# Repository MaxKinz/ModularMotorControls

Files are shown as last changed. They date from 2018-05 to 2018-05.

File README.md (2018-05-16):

"# ModularMotorControls" 
This is going to be a motor control project loosely based on the famous "VESC" project by benjamin vedder. 
So why another open source motor controller ? Well-mainly for modularity
The ultimate goal is to have a controller that does exactly what you need for a good price on every level wether you need to move some small 4000kv hobby rc motor or a full industrial Servo at 400V. Obviously the hardware required for the servo would be overkill and too expensive for the small motor while having additional limitations. 
Therefore hardware is going to be split into 3 categories that first have to be defined with all their requirements resulting in interfaces. A design requirement is that every implementation of one of those categories is compatible with every implementation of the two others so if for instance 3 implementations of each exist one could configure 27 different controllers. There will however be compatibility ranges between category 2 and 3 as it is impossible to completely seperate them. 

Here are the the categories :
  1. A logic board containing at least an STM32 microprocessor 
    -Variants with more or less calc power (closed loop control vs. open loop, BLDC or FOC..... Position/speed etc control) 
    -interfaces (CAN,I²C,UART,SPI....)
    -peripherals (IMUs,Bluetooth,ZigBee,LoRa or whatever comes to mind)    
    -may also be implemented breakout boards for readily available ebay bords
  
  2. A predriver stage containing MOSFET drivers as well as all the voltage "grooming" buck and boost converters (mainly different   
     different target Voltages)
     - "all in one"- solutions like the TI DRV8302
     - or discrete mosfet drivers and buck converters shunt amps 
     
  3. A power stage containing the main leads, the big input filter caps, and of course the MOSFETs/IGBTs, shunts,temp sense (mainly 
     different target currents but also voltages) 
     - all MOSFETs on one side or using both sides - different temp sensors,
     - SMD, THT , radiators,etc...
  
So as you can see I mainly just split up the usual components of a motor driver - big whoop - so what is this about ? 
Well - I would love to have defined interfaces between those parts. It would make it easy to reuse software that is otherwise rewritten over and over. It would also make it loads cheaper if by overloading your robot you yet again blew up a driver - and now conveniently only replace the power board (or if you are not so lucky power and predriver) 
All of my work on this will be open source. Since I plan on repurposing some of the VESC software which is based on ChibiOS and ChibiOS is GPL I might be forced to use GPL for the first iteration. However I am not a big fan of the agressive approach the GPL takes on open source which, if you are honest, resticts projects to hobby use as no employer I know wants his/her IP he payed you to create out there....so I would love to write some code under, for example, Apache liscense later in the process so truely anyone can use the controller even if you use it for work.

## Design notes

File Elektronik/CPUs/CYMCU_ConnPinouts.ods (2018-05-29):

 | Hall Sensors | Inc. Encoders | Mag enc. | I²C (gen.P.) | SPI (gen.P) | STEP/DIR | UART | AnalogIn
MCU Pin | PB6,PB7,PC11 | PB6,PB7,PC11 | PB6,PB7,PC11 | PA4,PA7 | PA4,PA5,PA6,PA7 | PA4/PA5 | PA4,PA7 | PC2
Interface | PIN HEADER 5x1 | PIN HEADER 5x1 | PIN HEADER 5x1 | PinHeader6x1 | PinHeader6x1 | PinHeader6x1 | PinHeader6x1 | PinHeader2x1
Notes | Only one sensor and one interface at a time ! - there will be two sensor ports though with filter (for Hall) and without (for incremental) but only one control signal connector

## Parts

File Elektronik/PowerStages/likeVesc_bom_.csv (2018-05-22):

Component | Description | Part | References | Value | Footprint | Quantity Per PCB | Datasheet
1 | Connector, double row, 02x10, pin header | CONN_02X10 | J1 | CONN_02X10 | Pin_Header_Straight_2x10_Pitch2.54mm | 1
2 | 2-pin screw terminal connector | Screw_Terminal_1x02 | J3 J4 | Screw_Terminal_1x02 | TerminalBlock_Altech_AK300-2_P5.00mm | 2
3 | 3-pin screw terminal connector | Screw_Terminal_1x03 | J2 | Screw_Terminal_1x03 | TerminalBlock_Altech_AK300-3_P5.00mm | 1
4 |  | MOSFET_N | Q1 Q2 Q3 Q4 Q5 Q6 | IRFS7530 | D2PAK-7-GDS | 6
5 |  | R-RESCUE-BLDC_4 | R3 R7 R11 | 39k | SMD-0603_r | 3
6 |  | R-RESCUE-BLDC_4 | R1 R2 R5 R6 R9 R10 | 4R7 | SMD-0603_r | 6
7 |  | SHUNT | R4 R8 | SHUNT | WSLP2726 | 2
Component Groups: | 7
Component Count: | 21
Fitted Components: | 21
Number of PCBs: | 1
Total components: | 21
Schematic Version:
Schematic Date:
BoM Date: | 22.05.2018 20:13:28
Schematic Source: | F:/git/ModularMotorControl/Elektronik/PowerStages/likeVesc.sch
KiCad Version: | Eeschema 4.0.6

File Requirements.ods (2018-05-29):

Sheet: Overview
This Document will hold the requirements for the Interfaces between the three categories of boards that make up a ModMot Controller It will also contain additional sheets for each implementation of any of the categories as made for a targeted application
 | Connections between logic and driver
 | going into logic | Name | Pin Number | Voltage/ref | Reason | Conclusion so far there are 18 connections necessary for the interface. As obviously some things may be added in the future a 2x15 pin header is chosen as the standard connection – the first 15 for incoming and the seconf 15 for outgoing connections on each board – pin numbers as in here top to bottom 1=VCC; 16=M1H
 |  | Vcc | 1 | 3.3V | MCU+Periph Power
 |  | Vsensors | 2 | 5V | for Periphery req. 5V
 |  | VsensHigh | 3 | 12V | for higher Voltage periphery such as inductive sensors or incremental encoders
 |  | GND | 4 | 0V | Ground reference
 |  | TempMosfets | 5 | SIGNAL | MosfetTempsense
 |  | VinSense | 6 | SIGNAL | Sense input voltage
 |  | SHUNT1 | 7 | SIGNAL | Current sense
 |  | SHUNT2 | 8 | SIGNAL | Current sense
 |  | SHUNT3 | 9 | SIGNAL | Current sense
 |  | Vsense1 | 10 | SIGNAL | Voltage sense
 |  | Vsense2 | 11 | SIGNAL | Voltage sense
 |  | Vsense3 | 12 | SIGNAL | Voltage sense
 | going into driver
 |  | M1H | 16 | FET SIGNAL | Switch Line one High side
 |  | M1L | 17 | FET SIGNAL | switch line one low side
 |  | M2H | 18 | FET SIGNAL | switch line two high side
 |  | M2L | 19 | FET SIGNAL | switch line two low side
 |  | M3H | 20 | FET SIGNAL | switch line three high side
 |  | M3L | 21 | FET SIGNAL | switch line three low side
 |  | Enable | 22 | SIGNAL | may be required by some drivers
 | Other Connections : | There may be plenty other connections such as Hall sensors, different input modes etc. but that is beyond the scope of this document. Only the essentials are recorded here as the goal is a standard cnnector layout used in different applications.
 | Connections from driver to power
 |  | M1H | 1 | FET DriveSignal |  | So far there are 16 connectinos and a 2x10 pin header is chosen. The power connections are missing as the driver outputs are already at the limit of a standard pin header so that a separate connection is needed
 |  | M1L | 2 | FET DriveSignal
 |  | M2H | 3 | FET DriveSignal
 |  | M2L | 4 | FET DriveSignal
 |  | M3H | 5 | FET DriveSignal
 |  | M3L | 6 | FET DriveSignal
 | Connections from power to driver
 |  | SH_1A | 11 | Shunt1+/Signal | if shuntamps are in Driver this is + else it carries the signal
 |  | SH_1B | 12 | Shunt1- | Shuntamps on Power -NC
 |  | SH_2A | 13 | Shunt2+/Signal
 |  | SH_2B | 14 | Shunt2-
 |  | H1VS | 15
 |  | H1Low | 16
 |  | H2VS | 17
 |  | H2LOW | 18
 |  | H3VS | 19
 |  | H3Low | 20

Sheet: Requirements_Logic_board
 |  |  | CPUs |  |  |  | Features |  |  | Interfaced accessories |  |  |  |  | Control interfaces
Design goals: | Description | Cheap/affordable | Use Ebay Board | STM32F1 /SoftwareBasis AutoQuad ESC32 | STM32F4 Software Basis VESC | STM32F4 Software Basis Odrive | Position Control | FOC | Dual Motor | Hall Sensors | Inc. Encoders | Mag enc. | I²C (gen.P.) | SPI (gen.P) | CAN | SPI | I²C | STEP/DIR | UART | ANALOG
Design 1 | BreakoutBoard for Bluepill to implement very cheap low power Servo controllers | x | x | x |  |  | x |  |  |  | x | x |  |  |  |  |  | x | x | -
Design 2 | BreakoutBoard for CYMCU407 | x | x |  | x |  | x | x |  | x | x | x | x | x |  |  |  | x | x | x

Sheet: PinoutsFirmwareBasis
Here we have the different pinouts for different firmwares
 |  |  |  |  | Autoquad ESC32 STM32F103 PIN Name | STM32F103 BluepillPinNumber
 | Vcc | 1 | 3.3V | MCU+Periph Power | -
 | Vsensors | 2 | 5V | for Periphery req. 5V | -
 | VsensHigh | 3 | 12V | for higher Voltage periphery such as inductive sensors or incremental encoders | -
 | GND | 4 | 0V | Ground reference | GND
 | TempMosfets | 5 | SIGNAL | MosfetTempsense | TODO
 | VinSense | 6 | SIGNAL | Sense input voltage | PA4
 | SHUNT1 | 7 | SIGNAL | Current sense | PA5
 | SHUNT2 | 8 | SIGNAL | Current sense | TODO
 | SHUNT3 | 9 | SIGNAL | Current sense | TODO
 | Vsense1 | 10 | SIGNAL | Voltage sense | PA1
 | Vsense2 | 11 | SIGNAL | Voltage sense | PA2
 | Vsense3 | 12 | SIGNAL | Voltage sense | PA3
 | M1H | 16 | FET SIGNAL | Switch Line one High side | PB6
 | M1L | 17 | FET SIGNAL | switch line one low side | PA7
 | M2H | 18 | FET SIGNAL | switch line two high side | PB7
 | M2L | 19 | FET SIGNAL | switch line two low side | PB0
 | M3H | 20 | FET SIGNAL | switch line three high side | PB8
 | M3L | 21 | FET SIGNAL | switch line three low side | PB1
 | Enable | 22 | SIGNAL | may be required by some drivers | TODO

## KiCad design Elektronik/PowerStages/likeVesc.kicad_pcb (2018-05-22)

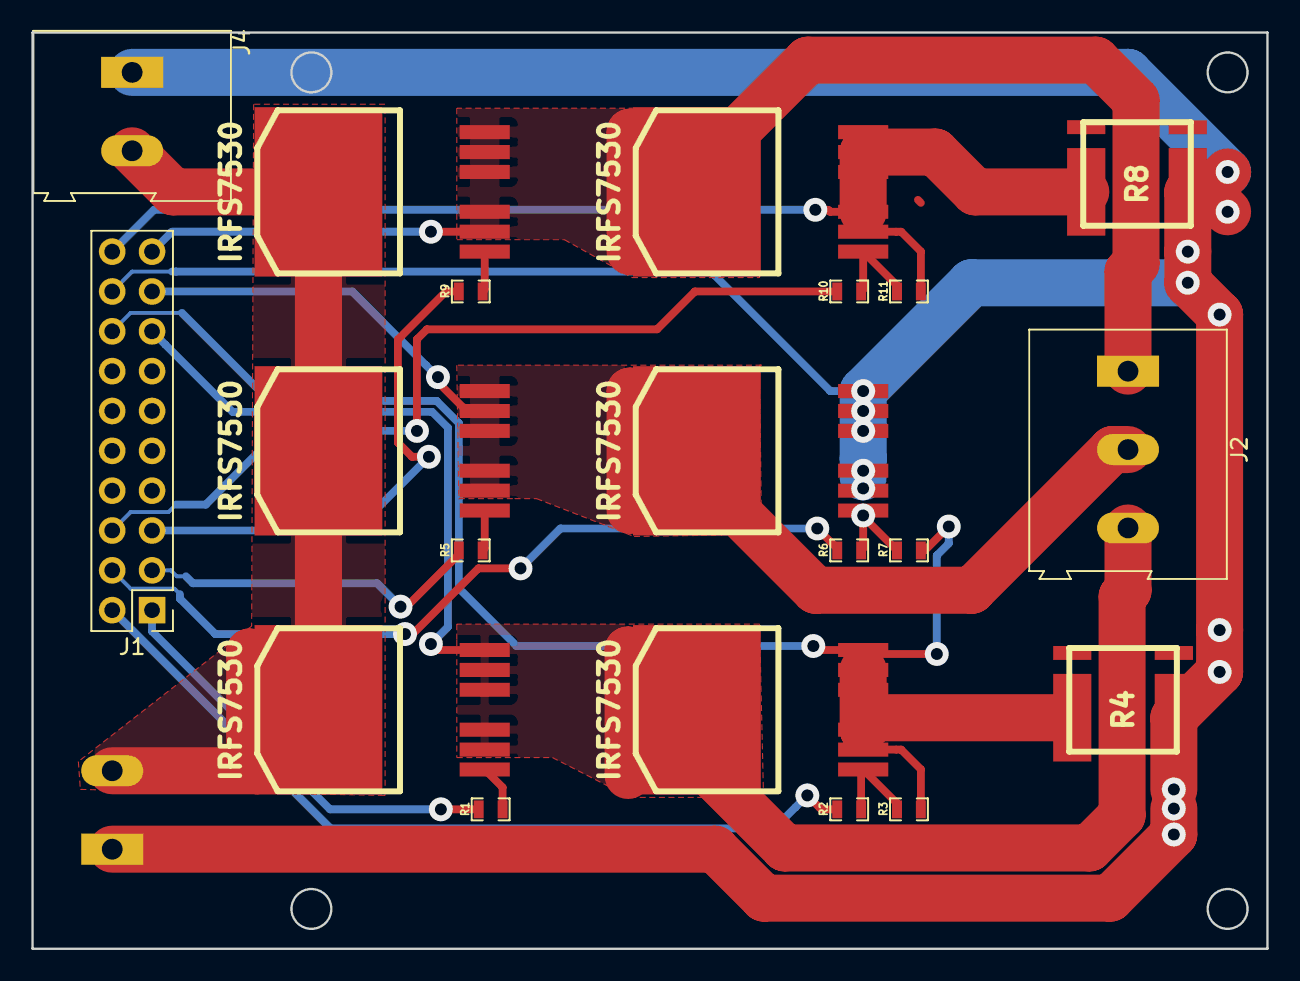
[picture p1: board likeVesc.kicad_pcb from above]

Board: 2 copper layers, 78.7 x 58.4 mm, 21 parts (1 on the bottom side), 19 nets.

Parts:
J1: CONN_02X10; Pin_Header_Straight_2x10_Pitch2.54mm
J2: Screw_Terminal_1x03; TerminalBlock_Altech_AK300-3_P5.00mm
J3, J4: Screw_Terminal_1x02; TerminalBlock_Altech_AK300-2_P5.00mm
Q1, Q2, Q3, Q4, Q5, Q6: IRFS7530; D2PAK-7-GDS
R1, R2, R5, R6, R9, R10: 4R7; SMD-0603_r
R3, R7, R11: 39k; SMD-0603_r
R4, R8: SHUNT; WSLP2726

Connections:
/BenMosfets/H1_LOW: J1.16, Q2.S, R3.1, R4.1, R7.1
/BenMosfets/H1_VS: J1.15, J2.3, Q1.S, Q2.D
/BenMosfets/H2_VS: J1.17, J2.2, Q3.S, Q4.D
/BenMosfets/H3_LOW: J1.20, Q6.S, R8.1, R11.1
/BenMosfets/H3_VS: J1.19, J2.1, Q5.S, Q6.D
/BenMosfets/M_H1: J1.1, R1.2
/BenMosfets/M_H2: J1.3, R5.2
/BenMosfets/M_H3: J1.5, R9.2
/BenMosfets/M_L1: J1.2, R2.2
/BenMosfets/M_L2: J1.4, R6.2
/BenMosfets/M_L3: J1.6, R10.2
GND: J1.18, J3.1, J4.1, Q4.S, R4.2, R8.2
unnamed: Q1.G, R1.1
unnamed: Q2.G, R2.1, R3.2
unnamed: Q3.G, R5.1
unnamed: Q4.G, R6.1, R7.2
unnamed: Q5.G, R9.1
unnamed: Q6.G, R10.1, R11.2
V_SUPPLY: J3.2, J4.2, Q1.D, Q3.D, Q5.D

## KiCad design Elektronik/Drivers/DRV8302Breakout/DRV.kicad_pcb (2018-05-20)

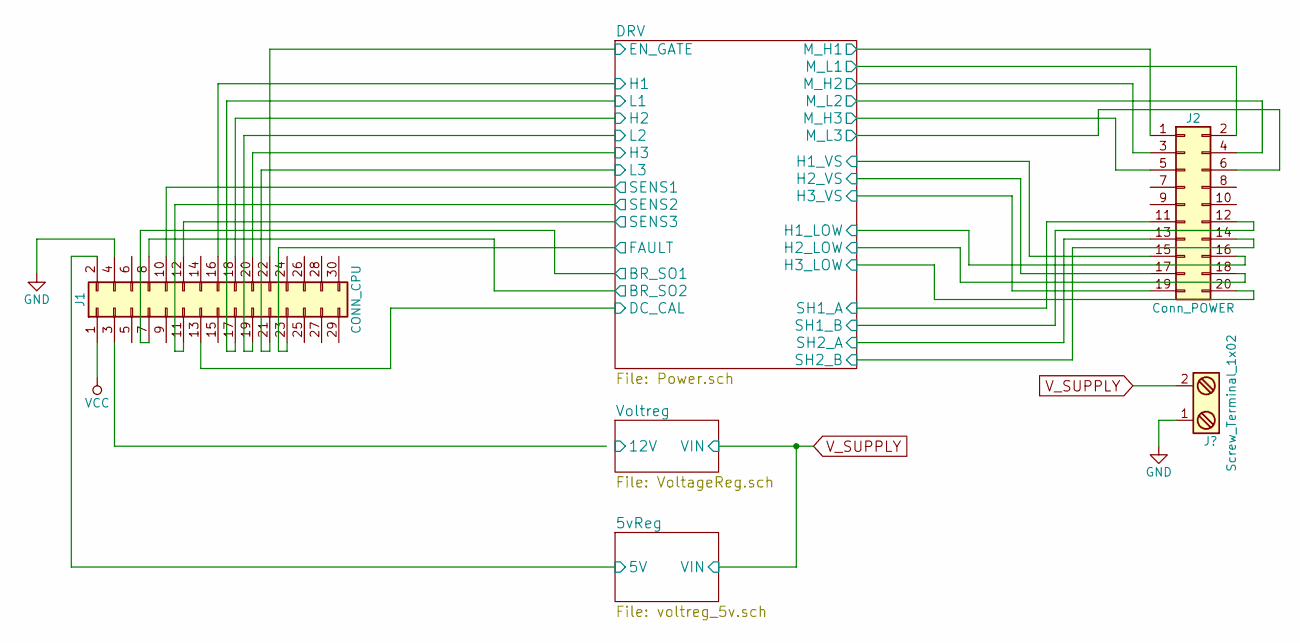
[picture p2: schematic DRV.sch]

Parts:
J1: CONN_CPU; Pin_Header_Straight_2x15_Pitch2.54mm
J2: Conn_POWER; Pin_Header_Straight_2x10_Pitch2.54mm

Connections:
/5vReg/5V: J1.2; also elsewhere on the board
/DRV/BR_SO1: J1.7; also elsewhere on the board
/DRV/BR_SO2: J1.8; also elsewhere on the board
/DRV/DC_CAL: J1.13; also elsewhere on the board
/DRV/EN_GATE: J1.22; also elsewhere on the board
/DRV/FAULT: J1.23; also elsewhere on the board
/DRV/H1: J1.16; also elsewhere on the board
/DRV/H1_LOW: J2.16; also elsewhere on the board
/DRV/H1_VS: J2.15; also elsewhere on the board
/DRV/H2: J1.18; also elsewhere on the board
/DRV/H2_LOW: J2.18; also elsewhere on the board
/DRV/H2_VS: J2.17; also elsewhere on the board
/DRV/H3: J1.20; also elsewhere on the board
/DRV/H3_LOW: J2.20; also elsewhere on the board
/DRV/H3_VS: J2.19; also elsewhere on the board
/DRV/L1: J1.17; also elsewhere on the board
/DRV/L2: J1.19; also elsewhere on the board
/DRV/L3: J1.21; also elsewhere on the board
/DRV/M_H1: J2.1; also elsewhere on the board
/DRV/M_H2: J2.3; also elsewhere on the board
/DRV/M_H3: J2.5; also elsewhere on the board
/DRV/M_L1: J2.2; also elsewhere on the board
/DRV/M_L2: J2.4; also elsewhere on the board
/DRV/M_L3: J2.6; also elsewhere on the board
/DRV/SENS1: J1.10; also elsewhere on the board
/DRV/SENS2: J1.11; also elsewhere on the board
/DRV/SENS3: J1.12; also elsewhere on the board
/DRV/SH1_A: J2.11; also elsewhere on the board
/DRV/SH1_B: J2.12; also elsewhere on the board
/DRV/SH2_A: J2.13; also elsewhere on the board
/DRV/SH2_B: J2.14; also elsewhere on the board
GND: J1.4; also elsewhere on the board
VCC: J1.1; also elsewhere on the board

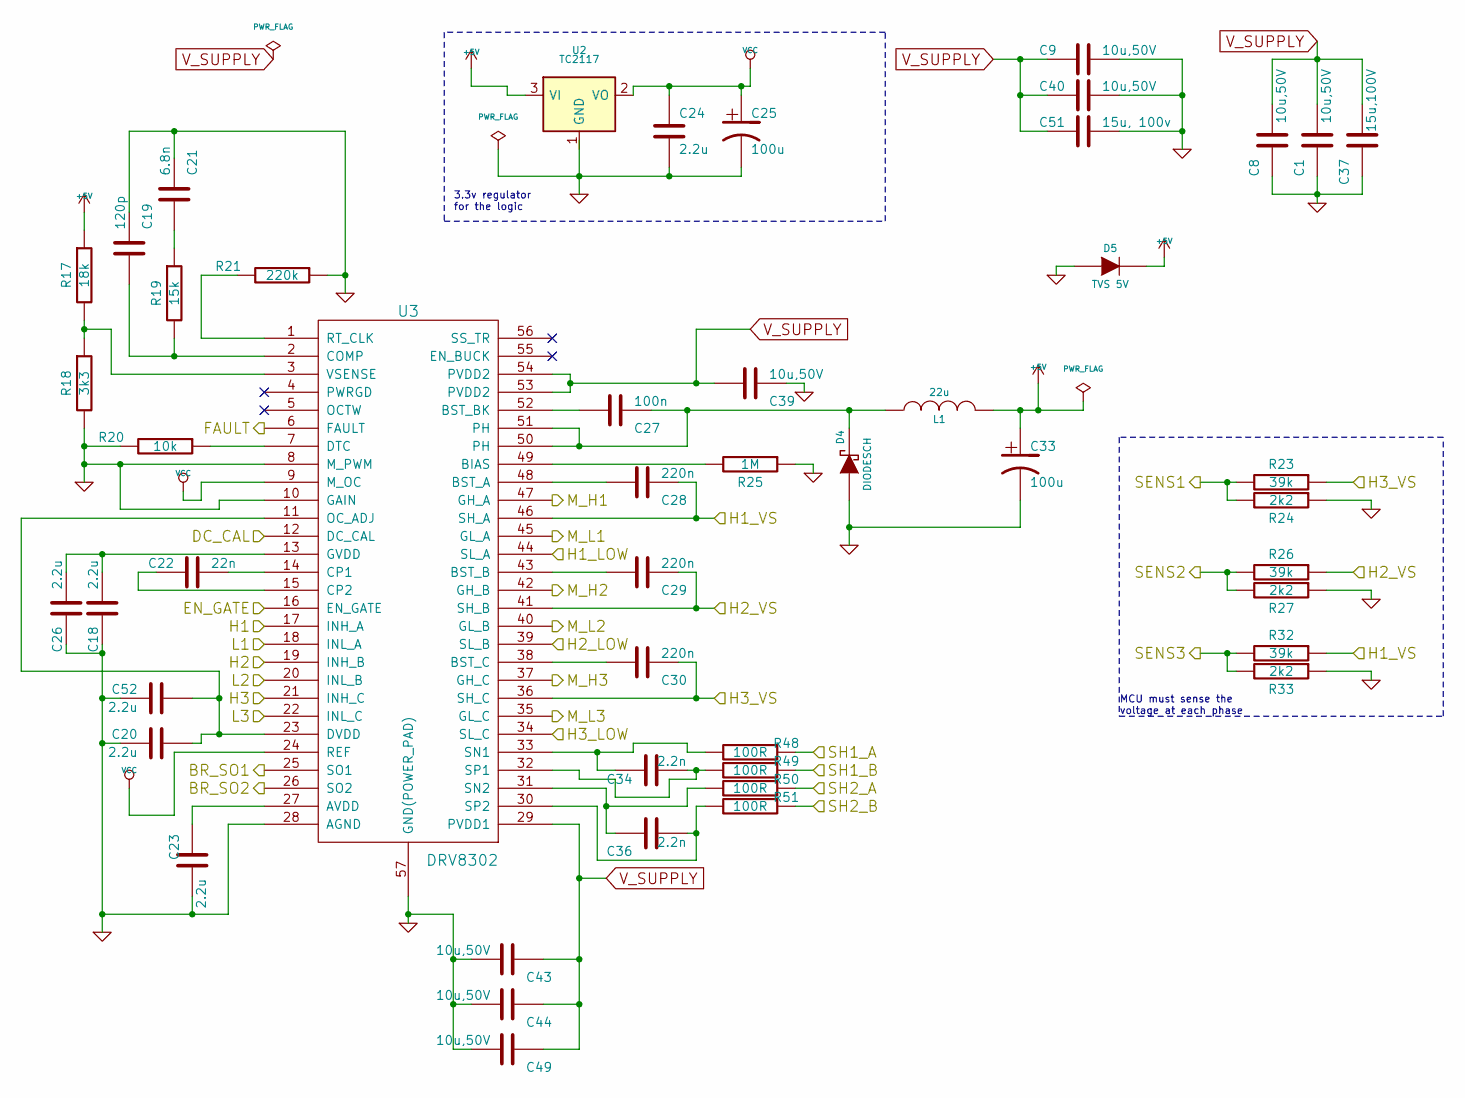
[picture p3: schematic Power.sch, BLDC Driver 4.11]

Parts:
C1, C8, C9, C39, C40, C43, C44, C49: 10u,50V; SMD-1206
C18, C20, C23, C24, C26, C52: 2.2u; SMD-0603_c
C19: 120p; SMD-0603_c
C21: 6.8n; SMD-0603_c
C22: 22n; SMD-0603_c
C25, C33: 100u; c_tant_B
C27: 100n; SMD-0603_c
C28, C29, C30: 220n; SMD-0603_c
C34, C36: 2.2n; SMD-0603_c
C37: 15u,100V; c_2220
C51: 15u, 100v; c_2220
D4: DIODESCH; SMA_Handsoldering
D5: TVS 5V; do214ac
L1: 22u; inductor_smd_8x5mm
R17: 18k; SMD-0603_r
R18: 3k3; SMD-0603_r
R19: 15k; SMD-0603_r
R20: 10k; SMD-0603_r
R21: 220k; SMD-0603_r
R23, R26, R32: 39k; SMD-0603_r
R24, R27, R33: 2k2; SMD-0603_r
R25: 1M; SMD-0603_r
R48, R49, R50, R51: 100R; SMD-0603_r
U2: TC2117; SOT-223
U3: DRV8302; TSSOP-56-PP

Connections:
+5V: C33.1, D5.2 (K), L1.2, R17.1, U2.3 (VI)
/DRV/BR_SO1: U3.25 (SO1); also elsewhere on the board
/DRV/BR_SO2: U3.26 (SO2); also elsewhere on the board
/DRV/DC_CAL: U3.12 (DC_CAL); also elsewhere on the board
/DRV/EN_GATE: U3.16 (EN_GATE); also elsewhere on the board
/DRV/FAULT: U3.6 (FAULT); also elsewhere on the board
/DRV/H1: U3.17 (INH_A); also elsewhere on the board
/DRV/H1_LOW: U3.44 (SL_A); also elsewhere on the board
/DRV/H1_VS: C28.1, R32.1, U3.46 (SH_A); also elsewhere on the board
/DRV/H2: U3.19 (INH_B); also elsewhere on the board
/DRV/H2_LOW: U3.39 (SL_B); also elsewhere on the board
/DRV/H2_VS: C29.1, R26.1, U3.41 (SH_B); also elsewhere on the board
/DRV/H3: U3.21 (INH_C); also elsewhere on the board
/DRV/H3_LOW: U3.34 (SL_C); also elsewhere on the board
/DRV/H3_VS: C30.1, R23.1, U3.36 (SH_C); also elsewhere on the board
/DRV/L1: U3.18 (INL_A); also elsewhere on the board
/DRV/L2: U3.20 (INL_B); also elsewhere on the board
/DRV/L3: U3.22 (INL_C); also elsewhere on the board
/DRV/M_H1: U3.47 (GH_A); also elsewhere on the board
/DRV/M_H2: U3.42 (GH_B); also elsewhere on the board
/DRV/M_H3: U3.37 (GH_C); also elsewhere on the board
/DRV/M_L1: U3.45 (GL_A); also elsewhere on the board
/DRV/M_L2: U3.40 (GL_B); also elsewhere on the board
/DRV/M_L3: U3.35 (GL_C); also elsewhere on the board
/DRV/SENS1: R23.2, R24.2; also elsewhere on the board
/DRV/SENS2: R26.2, R27.2; also elsewhere on the board
/DRV/SENS3: R32.2, R33.2; also elsewhere on the board
/DRV/SH1_A: R48.1; also elsewhere on the board
/DRV/SH1_B: R49.1; also elsewhere on the board
/DRV/SH2_A: R50.1; also elsewhere on the board
/DRV/SH2_B: R51.1; also elsewhere on the board
GND: C1.1, C8.1, C9.1, C18.2, C19.1, C20.1, C21.1, C23.1, C24.2, C25.2, C26.2, C33.2, C37.1, C39.1, C40.1, C43.2, C44.2, C49.2, C51.1, C52.1, D4.1 (A), D5.1 (A), R18.2, R20.2, R21.1, R24.1, R25.1, R27.1, R33.1, U3.8 (M_PWM), U3.10 (GAIN), U3.28 (AGND), U3.57 (GND(POWER_PAD)); also elsewhere on the board
unnamed: C18.1, C26.1, U3.13 (GVDD)
unnamed: C19.2, R19.2, U3.2 (COMP)
unnamed: C20.2, C52.2, U3.11 (OC_ADJ), U3.23 (DVDD)
unnamed: C21.2, R19.1
unnamed: C22.1, U3.14 (CP1)
unnamed: C22.2, U3.15 (CP2)
unnamed: C23.2, U3.27 (AVDD)
unnamed: C27.1, D4.2 (K), L1.1, U3.50 (PH), U3.51 (PH)
unnamed: C27.2, U3.52 (BST_BK)
unnamed: C28.2, U3.48 (BST_A)
unnamed: C29.2, U3.43 (BST_B)
unnamed: C30.2, U3.38 (BST_C)
unnamed: C34.1, R48.2, U3.33 (SN1)
unnamed: C34.2, R49.2, U3.32 (SP1)
unnamed: C36.1, R50.2, U3.31 (SN2)
unnamed: C36.2, R51.2, U3.30 (SP2)
unnamed: R17.2, R18.1, U3.3 (VSENSE)
unnamed: R20.1, U3.7 (DTC)
unnamed: R21.2, U3.1 (RT_CLK)
unnamed: R25.2, U3.49 (BIAS)
VCC: C24.1, C25.1, U2.2 (VO), U3.9 (M_OC), U3.24 (REF); also elsewhere on the board
V_SUPPLY: C1.2, C8.2, C9.2, C37.2, C39.2, C40.2, C43.1, C44.1, C49.1, C51.2, U3.29 (PVDD1), U3.53 (PVDD2), U3.54 (PVDD2); also elsewhere on the board

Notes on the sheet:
MCU must sense the voltage at each phase
3.3v regulator for the logic

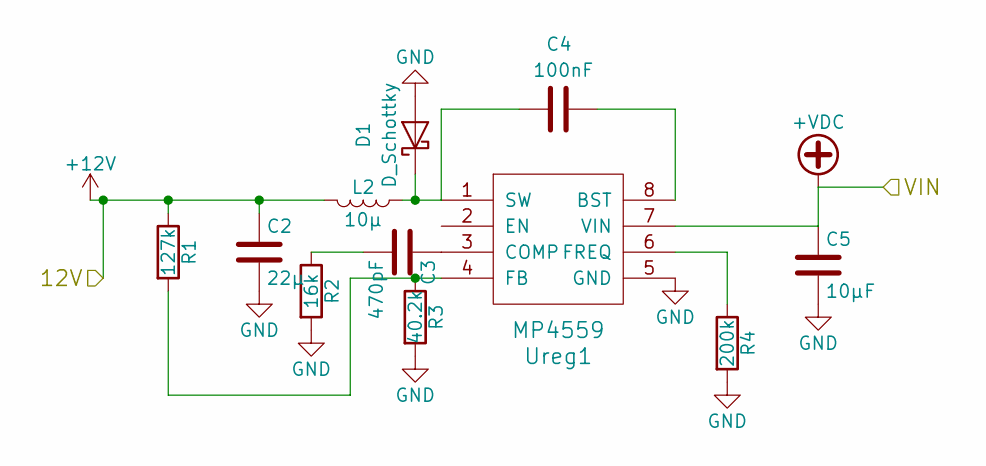
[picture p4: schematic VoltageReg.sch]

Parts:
C2: 22μ; C_2220
C3: 470pF; C_0603
C4: 100nF; C_0805
C5: 10μF; C_2225_HandSoldering
D1: D_Schottky; D_0603
L2: 10μ; inductor_smd_8x5mm
R1: 127k; R_0603
R2: 16k; R_0603
R3: 40.2k; R_0603
R4: 200k; R_0603
Ureg1: MP4559; SO-8_5.3x6.2mm_Pitch1.27mm

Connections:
+12V: C2.1, L2.2, R1.1
GND: C2.2, C5.2, D1.2 (A), R2.2, R3.2, R4.2, Ureg1.5 (GND); also elsewhere on the board
unnamed: C3.1, Ureg1.3 (COMP)
unnamed: C3.2, R2.1
unnamed: C4.1, Ureg1.8 (BST)
unnamed: C4.2, D1.1 (K), L2.1, Ureg1.1 (SW)
unnamed: R1.2, R3.1, Ureg1.4 (FB)
unnamed: R4.1, Ureg1.6 (FREQ)
V_SUPPLY: C5.1, Ureg1.7 (VIN); also elsewhere on the board

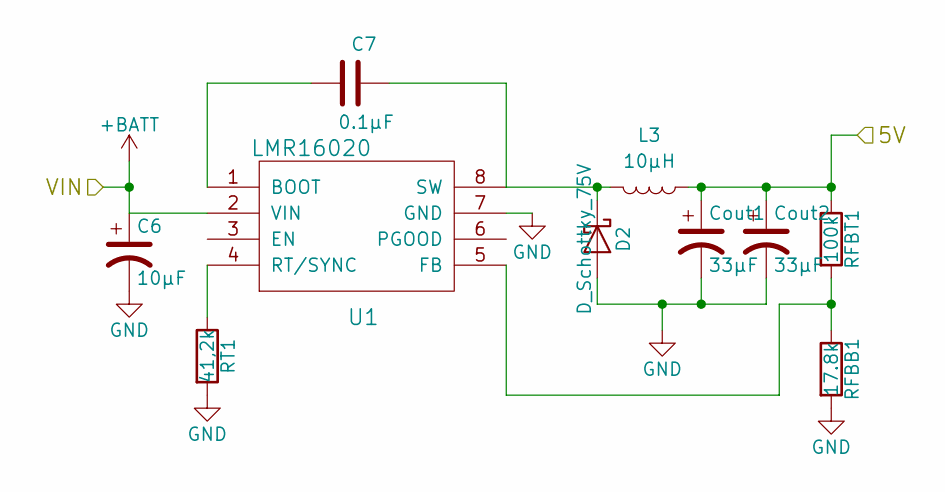
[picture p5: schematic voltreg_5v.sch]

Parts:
C6: 10μF; CP_Elec_5x5.3
C7: 0.1μF; C_0805
Cout1, Cout2: 33μF; CP_Elec_5x5.3
D2: D_Schottky_75V; D_0805
L3: 10μH; inductor_smd_8x5mm
RFBB1: 17.8k; R_0805
RFBT1: 100k; R_0805
RT1: 41,2k; R_0805
U1: LMR16020; SOIC-8-N

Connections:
/5vReg/5V: Cout1.1, Cout2.1, L3.1, RFBT1.1; also elsewhere on the board
GND: C6.2, Cout1.2, Cout2.2, D2.2 (A), RFBB1.2, RT1.2, U1.7 (GND); also elsewhere on the board
unnamed: C7.1, D2.1 (K), L3.2, U1.8 (SW)
unnamed: C7.2, U1.1 (BOOT)
unnamed: RFBB1.1, RFBT1.2, U1.5 (FB)
unnamed: RT1.1, U1.4 (RT/SYNC)
V_SUPPLY: C6.1, U1.2 (VIN); also elsewhere on the board

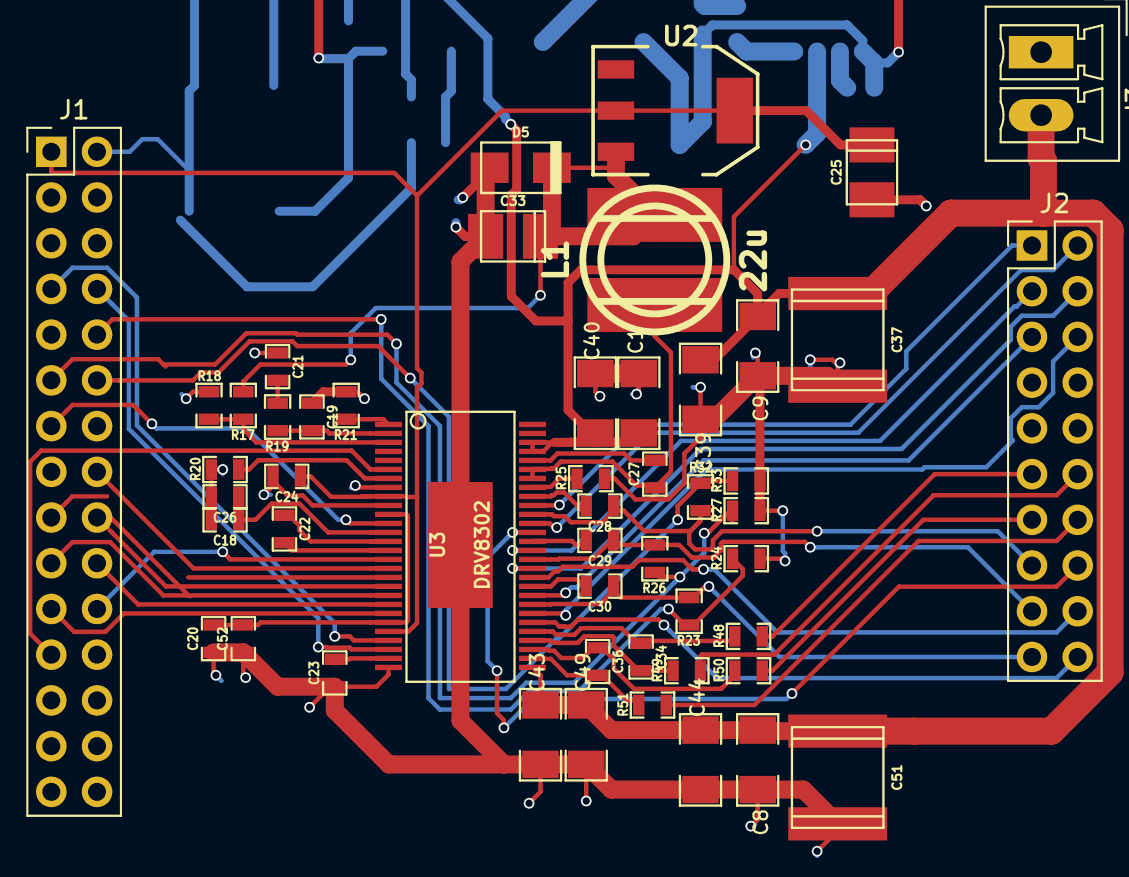
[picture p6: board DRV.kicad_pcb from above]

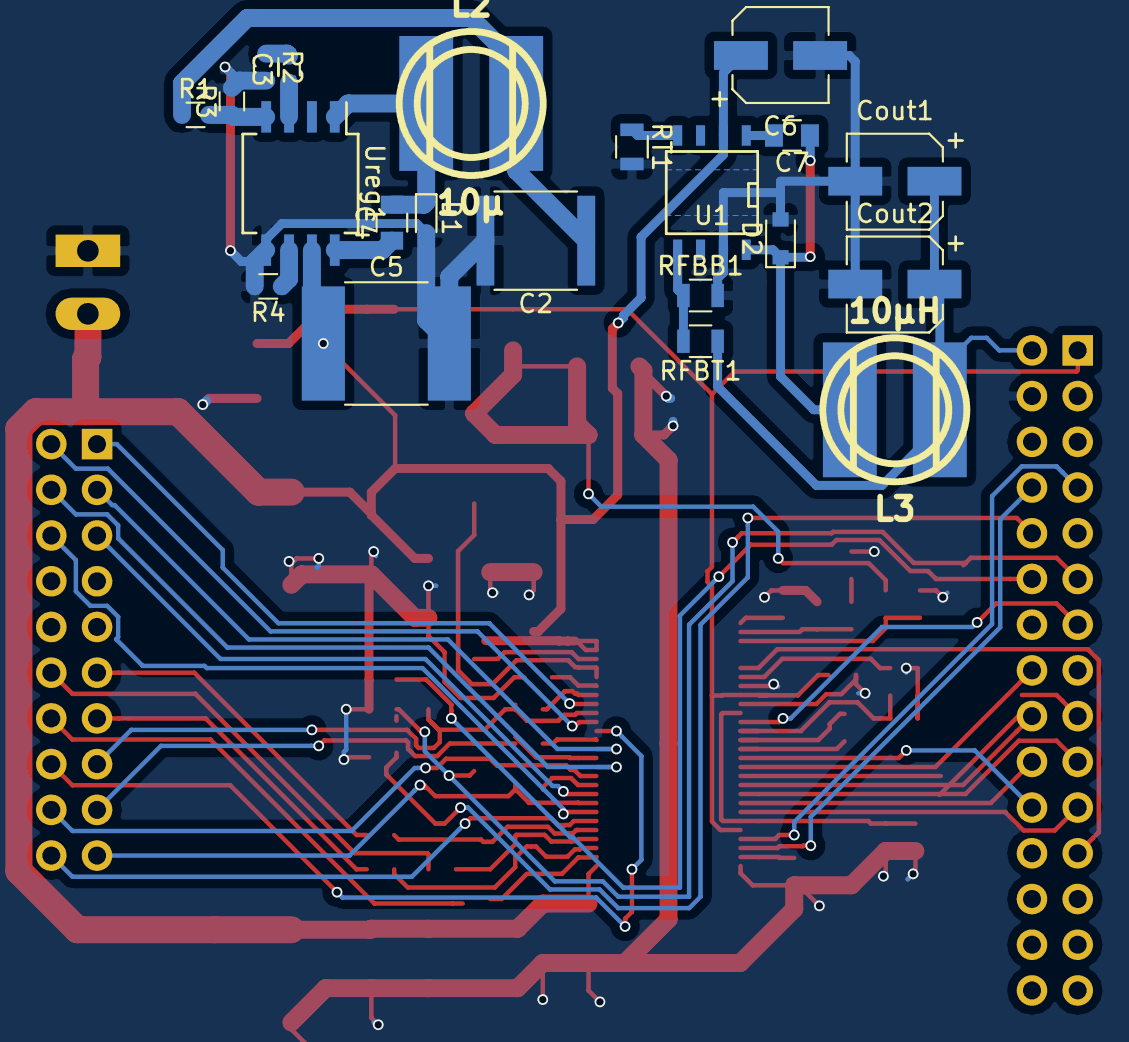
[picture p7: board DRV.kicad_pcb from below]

Board: 2 copper layers, 71 parts (21 on the bottom side), 66 nets.

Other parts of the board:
J3: Screw_Terminal_1x02; PhoenixContact_MCV-G_02x3.50mm_Vertical

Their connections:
GND: J3.1; also elsewhere on the board
V_SUPPLY: J3.2; also elsewhere on the board

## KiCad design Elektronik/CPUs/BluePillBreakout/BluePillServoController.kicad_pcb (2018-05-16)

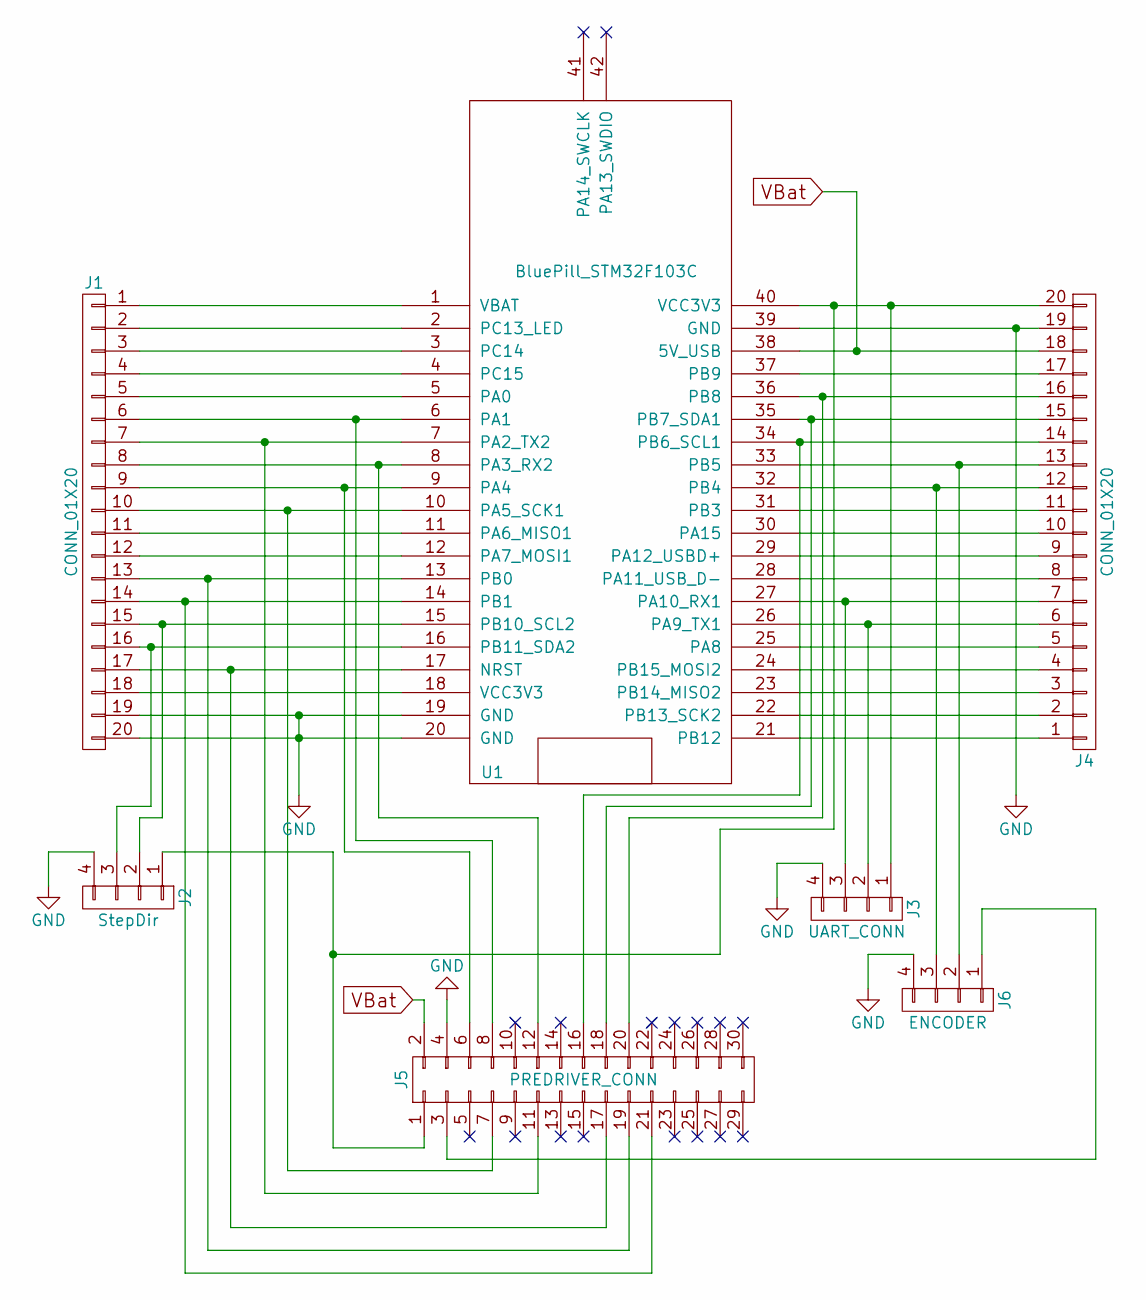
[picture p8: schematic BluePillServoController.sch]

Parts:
J1, J4: CONN_01X20; Pin_Header_Straight_1x20_Pitch2.54mm
J2: StepDir; Pin_Header_Straight_1x04_Pitch2.54mm
J3: UART_CONN; Pin_Header_Straight_1x04_Pitch2.54mm
J5: PREDRIVER_CONN; Pin_Header_Straight_2x15_Pitch2.54mm
J6: ENCODER; Pin_Header_Straight_1x04_Pitch2.54mm
U1: BluePill_STM32F103C

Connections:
GND: J1.19, J1.20, J2.4, J3.4, J4.19, J5.4, J6.4, U1.19 (GND), U1.20 (GND), U1.39 (GND)
unnamed: J1.1, U1.1 (VBAT)
unnamed: J1.2, U1.2 (PC13_LED)
unnamed: J1.3, U1.3 (PC14)
unnamed: J1.4, U1.4 (PC15)
unnamed: J1.5, U1.5 (PA0)
unnamed: J1.6, J5.8, U1.6 (PA1)
unnamed: J1.7, J5.11, U1.7 (PA2_TX2)
unnamed: J1.8, J5.12, U1.8 (PA3_RX2)
unnamed: J1.9, J5.6, U1.9 (PA4)
unnamed: J1.10, J5.7, U1.10 (PA5_SCK1)
unnamed: J1.11, U1.11 (PA6_MISO1)
unnamed: J1.12, U1.12 (PA7_MOSI1)
unnamed: J1.13, J5.19, U1.13 (PB0)
unnamed: J1.14, J5.21, U1.14 (PB1)
unnamed: J1.15, J2.2, U1.15 (PB10_SCL2)
unnamed: J1.16, J2.3, U1.16 (PB11_SDA2)
unnamed: J1.17, J5.17, U1.17 (NRST)
unnamed: J1.18, U1.18 (VCC3V3)
unnamed: J2.1, J3.1, J4.20, J5.1, U1.40 (VCC3V3)
unnamed: J3.2, J4.6, U1.26 (PA9_TX1)
unnamed: J3.3, J4.7, U1.27 (PA10_RX1)
unnamed: J4.1, U1.21 (PB12)
unnamed: J4.2, U1.22 (PB13_SCK2)
unnamed: J4.3, U1.23 (PB14_MISO2)
unnamed: J4.4, U1.24 (PB15_MOSI2)
unnamed: J4.5, U1.25 (PA8)
unnamed: J4.8, U1.28 (PA11_USB_D-)
unnamed: J4.9, U1.29 (PA12_USBD+)
unnamed: J4.10, U1.30 (PA15)
unnamed: J4.11, U1.31 (PB3)
unnamed: J4.12, J6.3, U1.32 (PB4)
unnamed: J4.13, J6.2, U1.33 (PB5)
unnamed: J4.14, J5.16, U1.34 (PB6_SCL1)
unnamed: J4.15, J5.18, U1.35 (PB7_SDA1)
unnamed: J4.16, J5.20, U1.36 (PB8)
unnamed: J4.17, U1.37 (PB9)
unnamed: J5.3, J6.1
VBat: J4.18, J5.2, U1.38 (5V_USB)

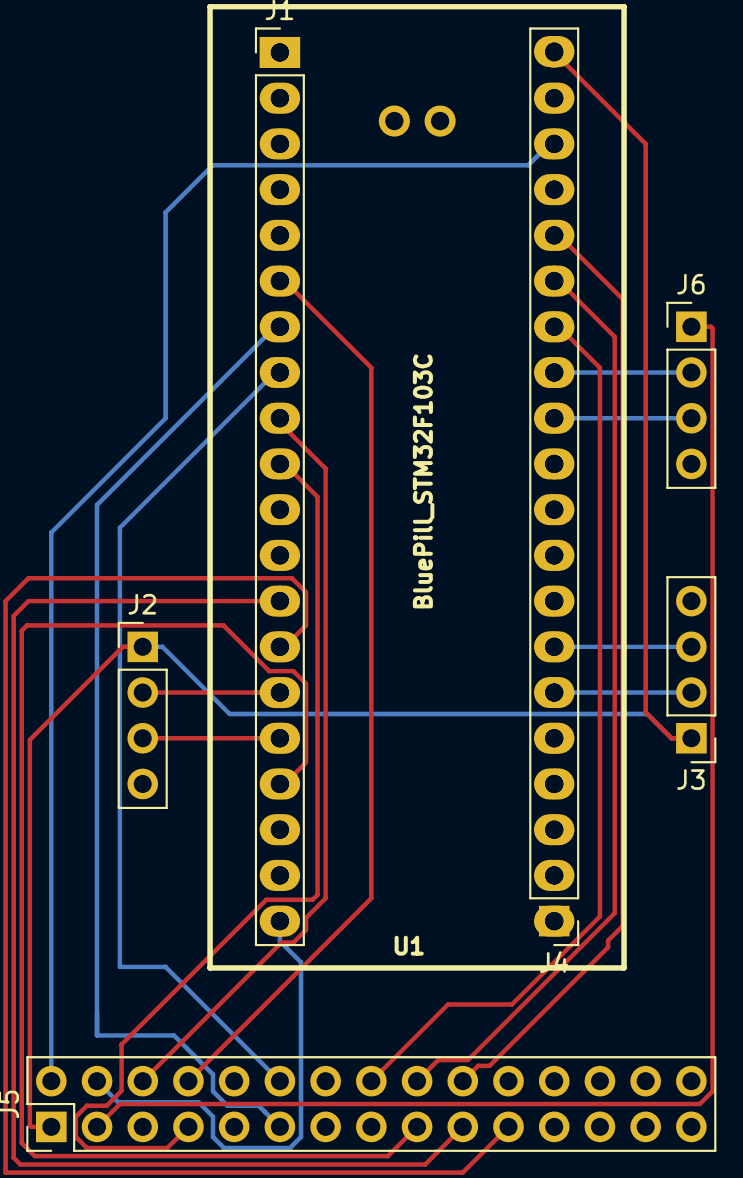
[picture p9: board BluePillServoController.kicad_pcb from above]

Board: 2 copper layers, 7 parts (0 on the bottom side), 39 nets.

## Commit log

2018-05-16 Defined some connections (See Requirements.ods) First Breakout for BluePill Routed
    [BluePillServoController.kicad_pcb, BluePillServoController.sch, Requirements.ods]
2018-05-19 Added some buck converter schematics
    [DRV.sch, Power.sch, suppliesFrom60V.kicad_pcb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]
2018-05-20 first driver pcb most things routed missnig power connector
    [DRV.kicad_pcb, DRV.sch, Power.sch]
2018-05-20 recommit as last didnt work
    [12VFrom60V.kicad_pcb, 12VFrom60V.sch, 5VFrom60V.kicad_pcb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]
2018-05-20 added power connection to driver board
    [DRV.kicad_pcb, DRV.sch, Requirements.ods]
2018-05-22 added a power stage
    [BensMosfetSchematic.sch, CJMCU_STM32F407_Breakout.kicad_pcb, CJMCU_STM32F407_Breakout.sch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]
